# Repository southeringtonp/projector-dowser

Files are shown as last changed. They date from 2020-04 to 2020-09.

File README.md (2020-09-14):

# What is this?

This is a proof-of-concept (but verified working) assembly
to create a projector dowser. It is controllable via DMX for
theatrical use, though has not (yet) been tested in a live
production.

This is a personal project and no warrantee or guarantee of any
kind is given. Use at your own risk.

A dowser can be built for under $100 with this approach, and
with some more work more cost can be shaved off. Commercially
versions typically run for $500 or more, though you likely
get what you pay for.

You will need a 3D Printer and assorted off-the-shelf parts. If you
want to edit the CAD files directly, you'll also need a recent copy
of Vectorworks, though you may be able to import the files into
other CAD software.

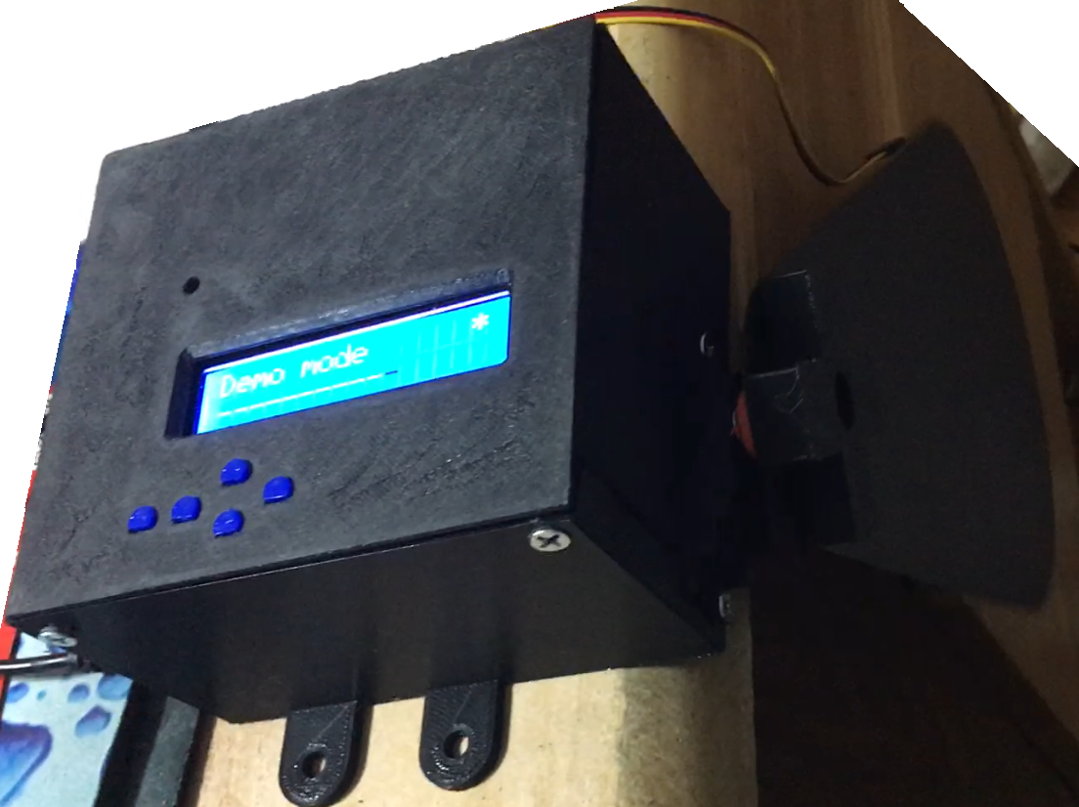
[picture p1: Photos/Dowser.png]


# Parts List

- Arduino Uno
  - https://store.arduino.cc/usa/arduino-uno-rev3

- DMX Shield for Arduino - Isolated (CTC-DRA-10-r2)
  - https://www.tindie.com/products/Conceptinetics/25kv-isolated-dmx-512-shield-for-arduino-r2/

- LCD Keypad Shield (e.g., DFR0009)*
  - Note: for button layout try to find the older version

- Servo Motor (e.g., HS-425BB)
  - https://www.amazon.com/Hitec-RCD-31425S-HS-425BB-Servo/dp/B0006O3WXM

- Stepdown Voltage Converter with barrel connector
  - https://www.amazon.com/gp/product/B01NALDSJ0

- Dowser Flag, premade (or make your own):
  - https://www.stagelightingstore.com/home/79056-city-theatrical-dowser-flag
  
- Pin Extenders, assorted**
  - https://www.amazon.com/Shield-Stacking-Header-Arduino-Pack/dp/B0756KRCFX/

*There seem to be different revisions of this out there. You may need to make
slight adjustments to the Arduino code and/or the 3d printed case top if you
have a different revision.

**for prototyping; a more permanent solution is recommended if you're going do to
this for serious work.

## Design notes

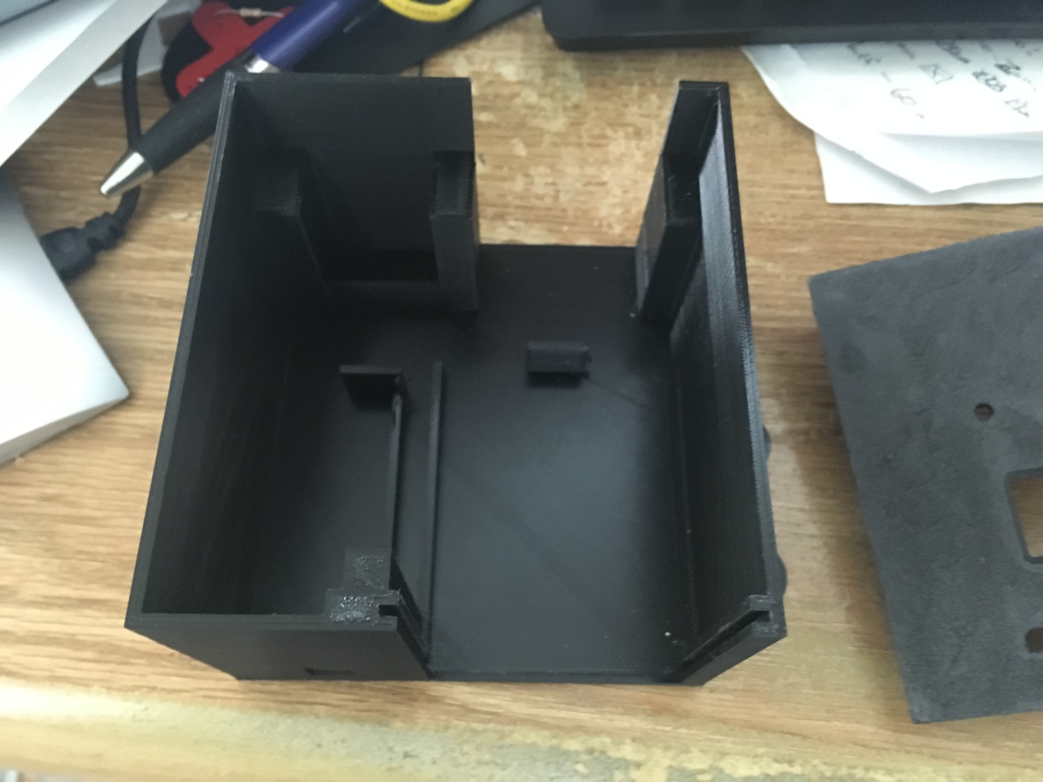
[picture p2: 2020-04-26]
Photos/CaseFrame.jpg

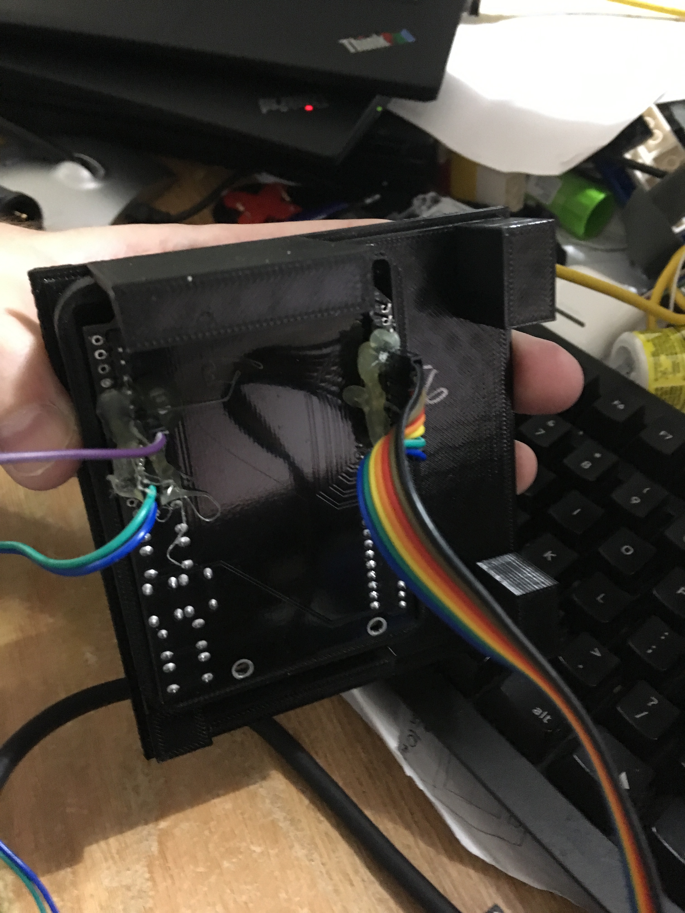
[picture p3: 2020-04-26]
Photos/Photo 31-07-2018, 3 14 43 pm.jpg

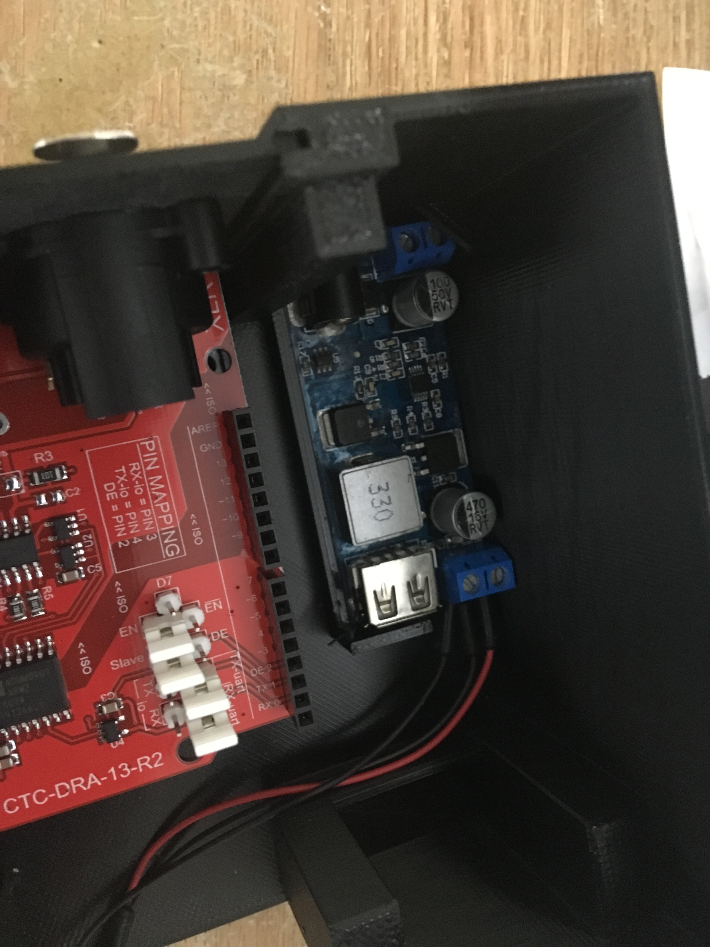
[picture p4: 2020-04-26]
Photos/Photo 01-08-2018, 1 33 56 pm.jpg

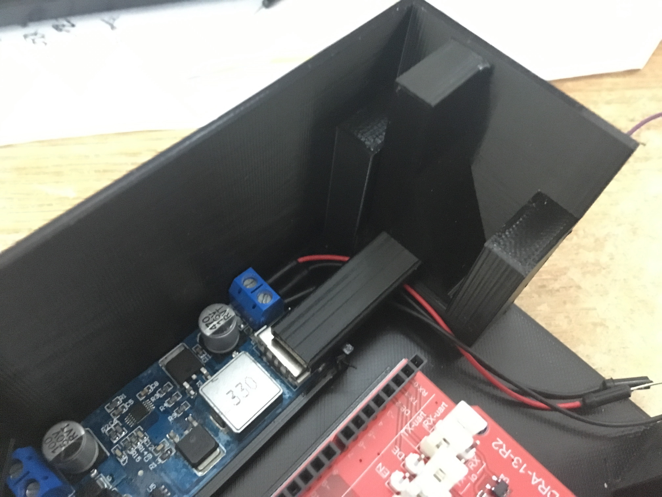
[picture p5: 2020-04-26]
Photos/Photo 01-08-2018, 1 34 14 pm.jpg

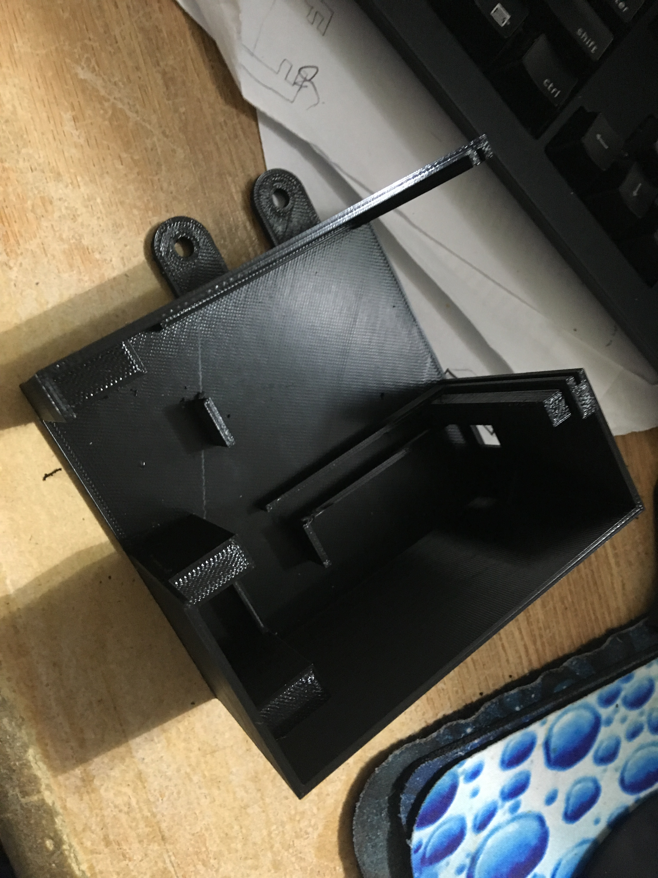
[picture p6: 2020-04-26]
Photos/CaseFrame2.jpg

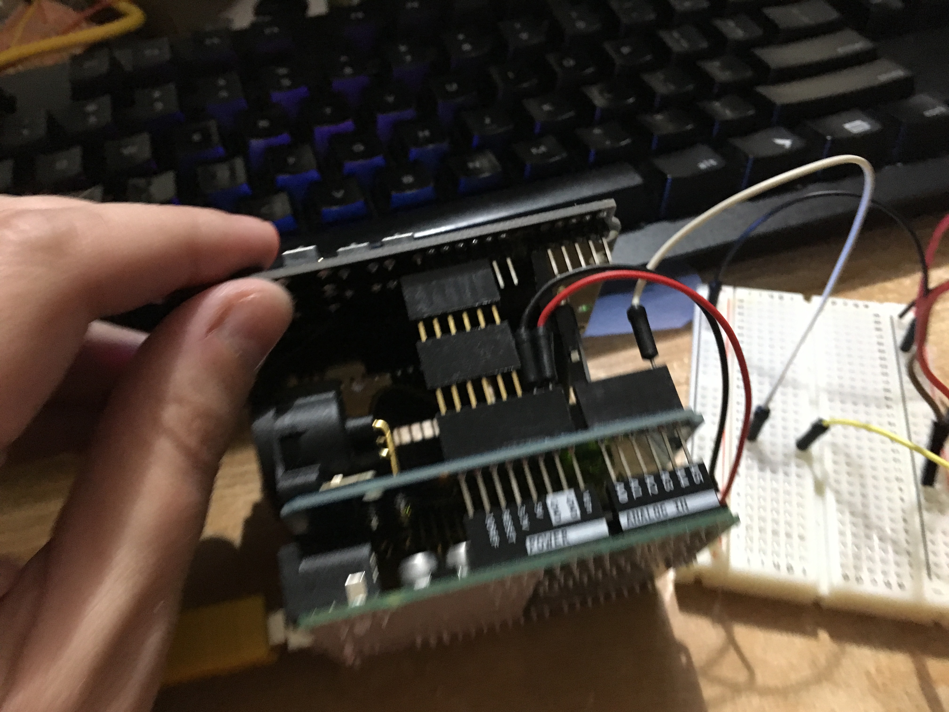
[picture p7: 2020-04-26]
Photos/Photo 21-07-2018, 1 58 40 am.jpg

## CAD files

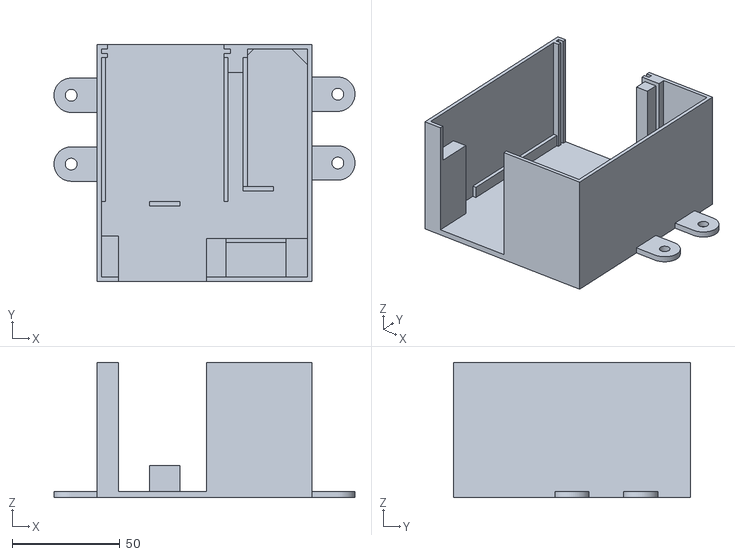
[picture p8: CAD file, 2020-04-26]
3dParts/Case Frame/Bottom8.stl
140.0 x 110.0 x 63.0

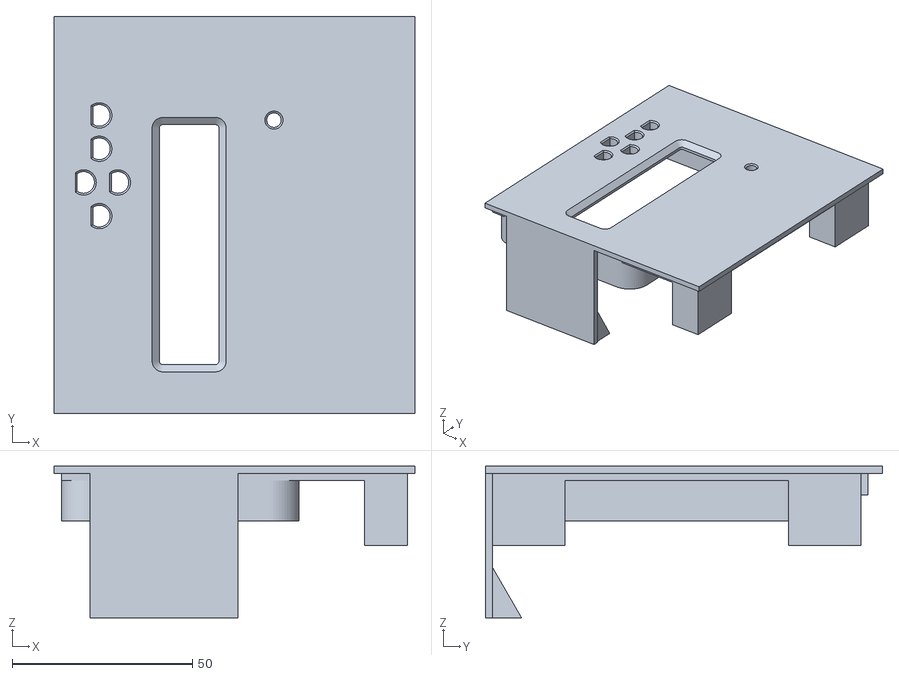
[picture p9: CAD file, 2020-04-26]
3dParts/Case Top/Top8.stl
100.0 x 110.0 x 42.0

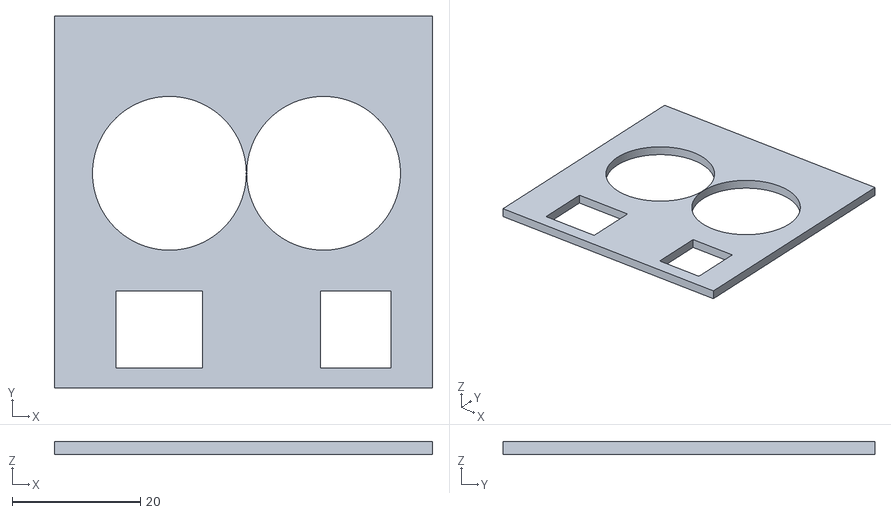
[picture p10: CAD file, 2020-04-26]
3dParts/Connector Plate/Faceplate2.stl
59.0 x 58.0 x 2.00

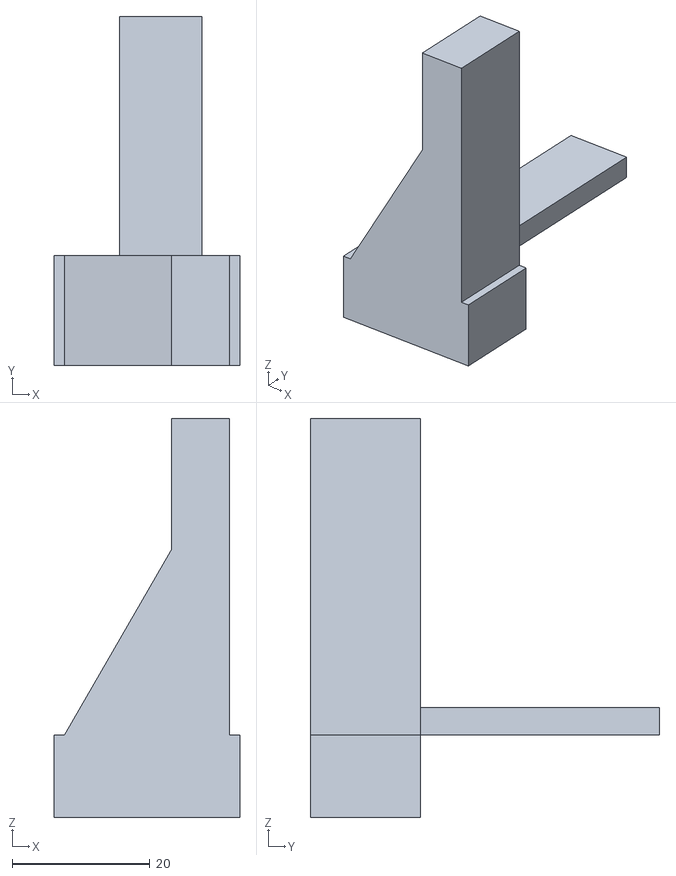
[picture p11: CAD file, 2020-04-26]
3dParts/Connector Plate/VRM Brace/VRM Brace 3.stl
27.0 x 50.8 x 58.0

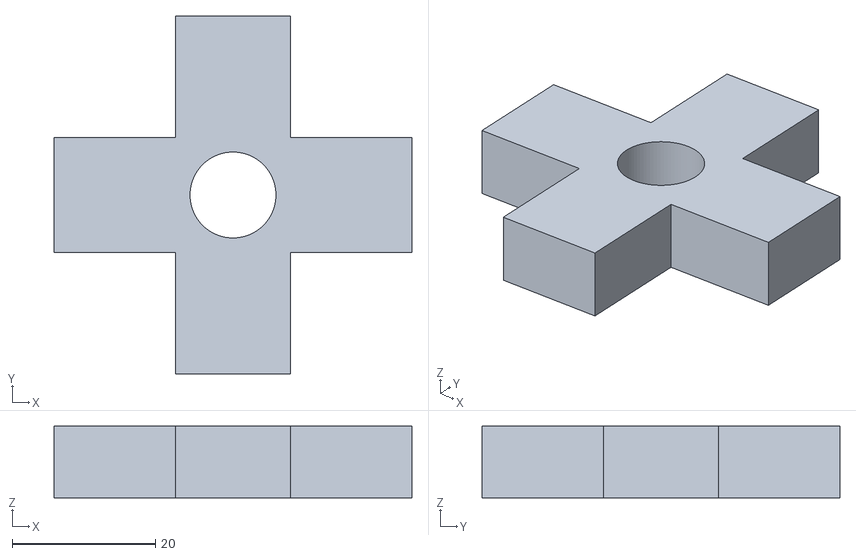
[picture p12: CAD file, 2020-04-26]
3dParts/Flag Brace/Cross.stl
50.0 x 50.0 x 10.0

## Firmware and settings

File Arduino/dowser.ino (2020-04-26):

#include <Servo.h>
#include <Conceptinetics.h>       // https://sourceforge.net/projects/dmxlibraryforar/files/
//#include <LiquidCrystal.h>       // https://www.dfrobot.com/wiki/index.php/Arduino_LCD_KeyPad_Shield_(SKU:_DFR0009)
#include <EEPROM.h>
#include <hd44780.h>
#include <hd44780ioClass/hd44780_pinIO.h>

#define BUTTON_PIN A0
#define SERVO_PIN A5
#define BACKLIGHT_PIN 10

#define DMX_TIMEOUT 5
#define DMX_SLAVE_CHANNELS   512

#define btnNONE   0
#define btnUP     1
#define btnDOWN   2
#define btnLEFT   3
#define btnRIGHT  4
#define btnSELECT 5

/*
 * (used by example from bperrybap)
 * Macros to safely turn on the backlight even with back BL hardware
 * These assume that the BL pin is not touched or used after RESET other
 * that by these macros.
 */
#define enableBacklight(pin) pinMode(pin, INPUT)
#define disableBacklight(pin) pinMode(pin, OUTPUT)


/*
 * GLOBALS
 */

Servo servo;
DMX_Slave dmx_slave (DMX_SLAVE_CHANNELS);
hd44780_pinIO lcd( 8, 9, 4, 5, 6, 7 );
//hd44780_pinIO lcd( 8, 9, 11, 5, 6, 7 );       // May need to move the connector from pin 4 to pin 11 to avoid conflict

int dmx_channel = 1;
int dmx_level = 0;
int dmx_scale_input = 1;               // Scale DMX input range (0-255) to match servo (0-180)
int default_on_signal_loss = 1;
unsigned long dmx_last_millis = 0;     // last time a dmx frame was received

int default_servo_position = 0;
int servo_position = 0;
int last_servo_position = -1;
int demo_mode_active = 0;

long int backlight_time = 0;





/************************************************************
 * Save and Restore Configuration
 ************************************************************/

// end with btnNONE instead of NULL
const int konami_sequence[] = { btnUP, btnUP, btnDOWN, btnDOWN, btnLEFT, btnRIGHT, btnLEFT, btnRIGHT, btnSELECT, btnNONE };
int check_konami(int keypress) {
  static int konami_progress = 0;
  if (keypress == btnNONE) return 0;

  if ( keypress == konami_sequence[konami_progress] ) {
    konami_progress++;
  } else {
    konami_progress = 0;
  }
  if ( konami_sequence[konami_progress] == btnNONE ) {
    konami_progress = 0;
    return 1;
  }
  return 0;
}

const char *secret[] = {
  "This is a test  " , "of the emergency",
  "easter egg      " , "system. In the  ",
  "event of a real " , "easter egg,     ",
  "this message    " , "would contain   ",
  NULL, NULL
};

void konami_message() {
  char **ptr;
  ptr = (char **)secret;
  while (*ptr != 0) {
    lcd.clear();
    lcd.setCursor(0,0);
    lcd.print(*ptr++);
    lcd.setCursor(0,1);
    lcd.print(*ptr++);
    delay(2600);
  }
  delay(2500);
  lcd.setCursor(0,0);
  lcd.print("                ");
  lcd.setCursor(0,1);
  lcd.print("                ");
  lcd.setCursor(15,1);
}

void dmx_secret_message() {
  if (dmx_channel == 232) {
    lcd.write("Happy Birthday!");
    delay(10000);
  } else if (dmx_channel == 255) {
    lcd.write("Happy");
    lcd.setCursor(0,1);
    lcd.write("towel day!!");
    delay(10000);
  }
}




/************************************************************
 * Save and Restore Configuration
 ************************************************************/

int check_range(int val, int min, int max, int dfl) {
  // Checks to see if a number is within the allowed range
  // Returns the number if it is valid, or returns default.
  if (val < min) return min;
  if (val > max) return min;
  return val;
}

void write_eeprom() {
  EEPROM.put(0, dmx_channel);
  EEPROM.put(4, default_servo_position);
  EEPROM.put(8, backlight_time);
  EEPROM.put(12, default_on_signal_loss);
  EEPROM.put(16, dmx_scale_input);
}

void read_eeprom() {
  // Read saved config from eeprom and apply defaults if data is invalid
  EEPROM.get(0, dmx_channel);
  EEPROM.get(4, default_servo_position);
  EEPROM.get(8, backlight_time);
  EEPROM.get(12, default_on_signal_loss);
  EEPROM.get(16, dmx_scale_input);
  dmx_channel = check_range(dmx_channel, 0, 255, 0);
  default_servo_position = check_range(default_servo_position, 0, 180, 0);
  backlight_time = check_range(backlight_time, 0, 15, 5);
  default_on_signal_loss = check_range(default_on_signal_loss, 0, 1, 1);
  dmx_scale_input = check_range(dmx_scale_input, 0, 1, 1);
}



/************************************************************
 * Timers and Support
 ************************************************************/

bool handleBacklightTimer(int keypress) {
  /* Manage timing for the LCD backlight;
   * returns true if the backlight gets turned on.
   * returns false if the backlight is already on or if it gets turned off
   * By convention, call with -1 to just extend the timer.
   */
  static unsigned long currentMillis = 0;
  static unsigned long backlightOffMillis = 10000;  // default value == time from reset to backlight off
  static bool backlight_enabled = true;

  if (backlight_time <= 0) return false;   // Always on
  
  currentMillis = millis();
  if (keypress != btnNONE) {
    // user pressed a key - make sure backlight is on
    backlightOffMillis = currentMillis + backlight_time*1000;
    if (!backlight_enabled) {
      enableBacklight(BACKLIGHT_PIN);
      backlight_enabled = true;
      return true;
    }
  } else {
    // no key pressed - turn backlight off if enough time has passed
    if (backlight_enabled && currentMillis > backlightOffMillis) {
      disableBacklight(BACKLIGHT_PIN);
      backlight_enabled = false;
    }
  }
  return false;
}


void OnFrameReceiveComplete (unsigned short channelsReceived) {
  /* Callback function that fires every time a full DMX frame is received */
  dmx_last_millis = millis();
  dmx_level = dmx_slave.getChannelValue(dmx_channel);
}

int get_keypress() {
    /* Observed raw values:
     *     Right  = 002         None   = 102
     *     Up     = 141         Down   = 325
     *     Left   = 502         Select = 739
     *     
     */
    static int previous_state = btnNONE;
    int current_state;
    int analog_value;

    analog_value = analogRead(BUTTON_PIN);
    if (analog_value > 900) current_state = btnNONE;
    else if (analog_value > 600) current_state = btnSELECT;
    else if (analog_value > 450) current_state = btnLEFT;
    else if (analog_value > 285) current_state = btnDOWN;
    else if (analog_value > 110) current_state = btnUP;
    else current_state = btnRIGHT;

    if (previous_state == current_state) return btnNONE;
    else {
      previous_state = current_state;
      return current_state; 
    }
}



/************************************************************
 * Menu Handlers
 ************************************************************/

typedef struct {
  int order;
  const char *title;
  bool (*handler)(int);
  bool should_write_eeprom;
} menu_descriptor;

menu_descriptor menus[] = {
  { 0, "               ", NULL,                     false  },
  { 1, "DMX Channel    ", menu_dmx_channel,          true  },
  { 2, "DMX Scaling    ", menu_dmx_input_scaling,    true  },
  { 3, "Start position ", menu_start_position,       true  },
  { 4, "On Signal Loss ", menu_dmx_signal_loss,      true  },
  { 5, "Backlight Time ", menu_backlight_time,       true  },
  { 6, "Demo mode      ", menu_demo_mode,            false },
  { 0 , NULL, NULL, false }
};



bool menu_dmx_channel(int keypress) {
  lcd.setCursor(0,1);
  lcd.print("Channel=" + String(dmx_channel) + "  ");
  if      (keypress == btnUP)    dmx_channel++;
  else if (keypress == btnDOWN)  dmx_channel--;
  else if (keypress == btnLEFT)  dmx_channel -= 10;
  else if (keypress == btnRIGHT) dmx_channel += 10;
  if (dmx_channel >= 512) dmx_channel = dmx_channel - 512;
  if (dmx_channel <= 0) dmx_channel = dmx_channel + 512;
  return false;
}


bool menu_dmx_input_scaling(int keypress) {
  if (keypress == btnUP || keypress == btnDOWN){
    dmx_scale_input = 1 - dmx_scale_input;
  }
  lcd.setCursor(0,1);
  if (dmx_scale_input) {
    lcd.print("DMX In Scale = Y");
  } else {
    lcd.print("DMX In Scale = N");
  }
  return false;
}

bool menu_dmx_signal_loss(int keypress) {
  if (keypress == btnUP || keypress == btnDOWN) {
    default_on_signal_loss = 1 - default_on_signal_loss;
  }
  lcd.setCursor(0,1);
  if (default_on_signal_loss) {
    lcd.print("Goto default   ");
  } else {
    lcd.print("Hold position  ");
  }
  return false;
}

bool menu_start_position(int keypress) {
  lcd.setCursor(0,1);
  lcd.print("Position=" + String(default_servo_position) + "  ");
  servo.write(default_servo_position);
  if      (keypress == btnUP)    default_servo_position++;
  else if (keypress == btnDOWN)  default_servo_position--;
  else if (keypress == btnLEFT)  default_servo_position -= 10;
  else if (keypress == btnRIGHT) default_servo_position += 10;
  if (default_servo_position >= 180) default_servo_position = default_servo_position - 180;
  if (default_servo_position < 0) default_servo_position = default_servo_position + 180;
  return false;
}

bool menu_backlight_time(int keypress) {
    if (keypress == btnUP) {
      backlight_time++;
      if (backlight_time == 16)      backlight_time = 30;
      else if (backlight_time == 31) backlight_time = 45;
      else if (backlight_time == 46) backlight_time = 60;
      else if (backlight_time > 60)  backlight_time = 0;
      else if (backlight_time == 1)  backlight_time = 5;
      handleBacklightTimer(-1);    
    } else if (keypress == btnDOWN) {
      backlight_time--;
      if (backlight_time < 0)        backlight_time = 60;
      else if (backlight_time == 59) backlight_time = 45;
      else if (backlight_time == 44) backlight_time = 30;
      else if (backlight_time == 29) backlight_time = 15;
      else if (backlight_time == 4)  backlight_time = 0;
      handleBacklightTimer(-1);    
    }
    lcd.setCursor(0,1);
    if (backlight_time > 0) {
      lcd.print(String(backlight_time) + "s        ");
    } else {
      lcd.print("Always on");
    }
    return false;
}


bool menu_demo_mode(int keypress) {
  static int demo_direction = 1;
  static int demo_position = 0;

  if (keypress == btnLEFT || keypress == btnRIGHT || keypress == btnUP || keypress == btnDOWN) {
    demo_mode_active = 1 - demo_mode_active;
  }
  if (!demo_mode_active) {
    lcd.setCursor(0,1);
    lcd.print("<demo inactive> ");
    return false;
  } else {
    // The demo is running.
    handleBacklightTimer(-1); // keep backlight always-on during demo
    demo_position = demo_position + demo_direction;
    if (demo_position == 180 || demo_position == 0) {
      demo_direction = 0 - demo_direction;
    }
    servo.write(demo_position);
    for (int i = 0; i < 16; i++) {
      lcd.setCursor(i,1);
      if ((demo_position*16)/180 > i) lcd.write("-");
      else lcd.write(" ");
    }
    delay(10);
    return true;
  }
}





/************************************************************
 * Core Arduino Functions
 ************************************************************/

void setup() {
  uint8_t heart[8] = {0x0,0xa,0x1f,0x1f,0xe,0x4,0x0};

  dmx_slave.enable();
  dmx_slave.setStartAddress(1);
  dmx_slave.onReceiveComplete(OnFrameReceiveComplete);
  
  read_eeprom();
  servo.attach(SERVO_PIN);

  pinMode(3, INPUT);              // DMX RX-io
  pinMode(BUTTON_PIN, INPUT);     // keypad's input
  lcd.begin(16,2);
  lcd.createChar(0, heart);       // load character to the LCD
  
  handleBacklightTimer(-1);
  dmx_secret_message();
  lcd.setCursor(0,0);
}



void loop() {
  unsigned long currentMillis = 0;
  static int current_menu = 0;
  bool dmx_signal;
  int skip_dmx;
  int keypress;  

  /* Handle Display and Config Menus */
  keypress = get_keypress();

  /* Check DMX Signal Status */
  currentMillis = millis();
  dmx_signal = (dmx_last_millis + DMX_TIMEOUT*1000 > currentMillis) ? true: false;

  /* Konami Code is important! */
  if (check_konami(keypress)) konami_message();
  
  // Suppress the key's normal function if it turned on the backlight
  if (handleBacklightTimer(keypress)) return;

  // Handle menu screens.
  // Either change to another menu or call the current menu's handler.
  if (keypress == btnSELECT) {
    // User pressed select - move to the next menu in the list
    if (menus[current_menu].should_write_eeprom) write_eeprom();
    demo_mode_active = 0;
    current_menu++;
    lcd.clear();
    if (menus[current_menu].handler == NULL) {
      current_menu = 0;
      return;
    } else {
      lcd.setCursor(0,0);
      lcd.print(menus[current_menu].title);
      lcd.setCursor(15,0);
      lcd.print("*");
      lcd.setCursor(0,1);
    }
  } else {
    // We are in a menu... let the menu handler deal with this.
    if (current_menu != 0) {
      skip_dmx = menus[current_menu].handler(keypress);
    }
  } 
  
  if (current_menu == 0) {
    // This is the normal display - just process and display DMX
    lcd.setCursor(0,0);
    lcd.print("DMX Channel=" + String(dmx_channel) + "  ");
    lcd.setCursor(0,1);
    if (!dmx_signal) {
      lcd.print("No DMX Signal   ");
    } else {
      lcd.print("DMX Level=" + String(dmx_level) + "  ");
    }
    lcd.setCursor(15,0);
    lcd.print(" ");
  }

  // Some menus will have handled DMX output themselves.
  // If a menu returned true above, skip_dmx will be set and we won't touch the servo here.
  if (skip_dmx) return;

  /* Routine I/O Processing */
  if (dmx_signal) {
    servo_position = dmx_level;
    if (dmx_scale_input) servo_position = servo_position * (180.0/255.0);
    if (servo_position > 180) servo_position = 180;
  } else if (default_on_signal_loss) {
    // We may or may not want to reset the position when DMX signal drops
    servo_position = default_servo_position;
  }
  
  if (servo_position != last_servo_position) {
    // Don't try to move the servo unless it actually needs to move.
    servo.write(servo_position);
    last_servo_position = servo_position;
  }
}
